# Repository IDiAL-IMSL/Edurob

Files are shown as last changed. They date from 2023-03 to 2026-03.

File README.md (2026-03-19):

# EduRobV2
[Homepage](https://www.imsl.fh-dortmund.de/mobile-roboter/edurob/)
## Educational robot with support for various drive kinematics

EduRob is a handy mobile robot specially designed for education. Through clever design, it is possible to cover different types of drives such as Mecanum, Omniwheel, and differential drive.



## Detailed information:

[Getting Started](Doc/README.md)

[Partslist](Doc/Partslist/README.md)

[PCB](https://github.com/IDiAL-IMSL/Edurob-PCB)

[CAD](https://github.com/IDiAL-IMSL/Edurob-CAD/README.md)

## Example projects:

[SLAM](Projects/SLAM/README.md)

[Line Follower](https://github.com/blssed/EduRob-LineFollower)

---

## Background

In the robotics lab, there is a wide range of different robots available for use in teaching and for the completion of thesis projects. However, they all share one major disadvantage: they prefer to drive themselves rather than being carried. As a result, their application is limited to the lab itself and adjacent rooms.

Especially for basic training in mobile robotics such as controlling different types of drives (Mecanum, Omniwheel, or differential drive), implementing control tasks, and connecting sensors, the experimental area of the robotics lab is not necessarily required. This led to the requirement of developing a flexible platform that can cover all types of drives, and small enough to be taken in a backpack to the home office.

# Possible configurations

EduRob can be equipped with three or four motors and different types of wheels. The motors can be flexibly reconnected by loosening two screws, and other wheels can be attached to the motor shaft.

## Mecanum 

With four motors at the four outer corners, EduRob can be turned into a robot with a classic Mecanum drive. The driving behavior is thus similar to that of OmniMan and the other Mecanum robots of the IMSL.



## Omniwheel with three wheels (120°)

With three motors, EduRob can simulate the classic omniwheel configuration. Three wheels rotated by 120° each allow for omnidirectional driving behavior.



## Omniwheel with four wheels (90°)

In addition to the classic arrangement with three omniwheels, EduRob can also simulate the special form with four omniwheels. Here, four omniwheels are arranged with a rotation of 90° to each other. In comparison to the Mecanum arrangement, the wheels are rotated by about 45°. In this configuration, EduRob can also be driven omnidirectionally.



## Differential drive or Skid-Steer drive

The driving behavior of the Pioneer robots in the IMSL inventory is made possible by the use of four wheels. Even though the arrangement of the wheels is similar to the Mecanum arrangement, sideways movement is not possible due to the use of classic wheels without freewheeling rollers. In addition to forward and backward movement and rotation around the center of the platform, driving in circular arcs is possible. This type of drive is also called Skid-Steer drive. Due to the 4x4 drive, this configuration is particularly suitable for rough terrain. The absence of freewheeling rollers on the wheels also means they are less likely to become contaminated or blocked.



By using two classic wheels and one or two non-driven Omniwheels, a proper differential drive is also possible. In this case, the rotation point moves to the midpoint between the two driven wheels. While this affects the robot's turning behavior (the front part swings out), it still maintains its limited range of movement (forward, backward, turning, and driving in circles). However, the "off-road" capability is reduced by the reduction to two driven wheels, and the use of Omniwheels increases the risk of contamination of free-rolling rollers.



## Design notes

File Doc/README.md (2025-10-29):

## QUICKSTART TO EDUROB V2

### Installation 

Software required:
- Arduino IDE (https://www.arduino.cc/en/software/) - tested with Arduino IDE 2.3.6
- optional: ROS2 Jazzy (https://docs.ros.org/en/jazzy/) - tested with Ubuntu 24.04 

Integration in Arduino IDE:
1. Clone the Repository and move the included library folders in `Edurob/libraries` to the local library folder of Arduino IDE, for instance `~/Arduino/libraries`
4. Insert "Addition boards manager URL": File → Preferences: `https://espressif.github.io/arduino-esp32/package_esp32_index.json`
5. Select board: Tools → Board →esp32 →`ESP32S3 Dev Module`
6. Select port: Tools → Port → for instance `/dev/ttyACM0`
7. Open the folder `Edurob` and open the Arduino sketch `Edurob.ino` in Arduino IDE
8. Modify the Arduino sketch according to your own preferences (see Usage below)
9. Verify and upload the Arduino sketch via USB-C port on Edurob V2 and hit the reset button on the robot to start the uploaded code

### Usage

Set configuration of the Edurob V2 in lines 6 to 10 of `parameter.h` to to define the kinematics of the robot and only comment out the one selected configuration (ideally matching the wheel configuration of the robot hardware):
```
// Set EduRob Configuration
#define MECANUM
// #define DIFF
// #define OMNI4
// #define OMNI3
```

Set line 4 of  `parameter.h` to disable or enable a wireless connection to ROS2 device (via micro_ros)

- disable: `//#define ROS_EN` 
	
	Add user code in the corresponding segment inside the loop function (lines 665 to 669) of `Edurob.ino`:
	```
	//#############-USER-CODE-START-#####################
  	// double tx = 0.0, ty = 0.0, theta = 0.0;
  	// robotSpeedSetpoint << tx, ty, theta;
	// #############-USER-CODE-END-#####################
	```

- enable: `#define ROS_EN`
	
	Set ROS2 enabled parameters in lines 14 to 19 of `parameter.h`:

	```
	#ifdef ROS_EN
	#define ROS_DOMAIN_ID 1
	#define WIFISSID "ESPNET"
	#define WIFIPASS "espnetwifikey"
	#define AGENT_IP "10.0.101.253"
	#define AGENT_PORT 8888
	```

	- set ROS_DOMAIN_ID (refers to https://docs.ros.org/en/jazzy/Concepts/Intermediate/About-Domain-ID.html)
	- set name and password of wifi
	- set ip address and port of micro_ros_agent on ROS2 Jazzy device in same network

	Installation of micro_ros_agent (refers to https://github.com/micro-ROS/micro_ros_setup) on ROS2 Jazzy device in same network in a ROS2 workspace folder (for instance ~/ros2_ws) in a terminal:

	```
	cd ~/ros2_ws
	sudo apt update
	sudo apt install python3-rosdep
	git clone -b jazzy https://github.com/micro-ROS/micro_ros_setup.git src/micro_ros_setup
	rosdep update && rosdep install --from-paths src --ignore-src -y
	sudo rosdep init
	rosdep update
	colcon build --symlink-install
	source install/local_setup.bash
	ros2 run micro_ros_setup create_agent_ws.sh
	ros2 run micro_ros_setup build_agent.sh
	source install/local_setup.bash
	```

	Start of micro_ros_agent on ROS2 Jazzy device with udp4 and defined AGENT_PORT parameters in a terminal:

	```
	ros2 run micro_ros_agent micro_ros_agent udp4 --port 8888
	```

	The terminal should output:

	```
	[1761729504.052943] info     | UDPv4AgentLinux.cpp | init                     | running...             | port: 8888
	[1761729504.055070] info     | Root.cpp           | set_verbose_level        | logger setup           | verbose_level: 4
	```

	Press the reset button on the robot. The terminal output will change if successful:

	```
	[1761729504.052943] info     | UDPv4AgentLinux.cpp | init                     | running...             | port: 8888
	[1761729504.055070] info     | Root.cpp           | set_verbose_level        | logger setup           | verbose_level: 4
	[1761729843.354045] info     | Root.cpp           | create_client            | create                 | client_key: 0x7A4912AF, session_id: 0x81
	[1761729843.355923] info     | SessionManager.hpp | establish_session        | session established    | client_key: 0x7A4912AF, address: 10.0.109.1:47138
	[1761729843.510983] info     | ProxyClient.cpp    | create_participant       | participant created    | client_key: 0x7A4912AF, participant_id: 0x000(1)
	[1761729843.574304] info     | ProxyClient.cpp    | create_topic             | topic created          | client_key: 0x7A4912AF, topic_id: 0x000(2), participant_id: 0x000(1)
	[1761729843.586440] info     | ProxyClient.cpp    | create_subscriber        | subscriber created     | client_key: 0x7A4912AF, subscriber_id: 0x000(4), participant_id: 0x000(1)
	[1761729843.594849] info     | ProxyClient.cpp    | create_datareader        | datareader created     | client_key: 0x7A4912AF, datareader_id: 0x000(6), subscriber_id: 0x000(4)
	[1761729843.601925] info     | ProxyClient.cpp    | create_topic             | topic created          | client_key: 0x7A4912AF, topic_id: 0x001(2), participant_id: 0x000(1)
	[1761729843.607856] info     | ProxyClient.cpp    | create_publisher         | publisher created      | client_key: 0x7A4912AF, publisher_id: 0x000(3), participant_id: 0x000(1)
	[1761729843.614818] info     | ProxyClient.cpp    | create_datawriter        | datawriter created     | client_key: 0x7A4912AF, datawriter_id: 0x000(5), publisher_id: 0x000(3)
	```

	The ROS2 terminal command `ros2 topic list` will show:

	```
	/cmd_vel
	/parameter_events
	/rosout
	/tf
	```

	The ROS2 terminal command `ros2 node list` will output `/EduRob_Node`. A following command `ros2 node info /EduRob_Node` will show that the node `/EduRob_Node` subscribed to the topic `/cmd_vel` and publishes the topic `/tf` as seen in the topic list before:

	```
	/EduRob_Node
	  Subscribers:
		/cmd_vel: geometry_msgs/msg/Twist
	  Publishers:
		/tf: tf2_msgs/msg/TFMessage
	```

	Since transformations are published via `/tf` and driving commands are sent in ROS2 via `/cmd_vel`, the robot is ready to be controlled, among other things, via a teleoperation node such as teleop_twist_keyboard.

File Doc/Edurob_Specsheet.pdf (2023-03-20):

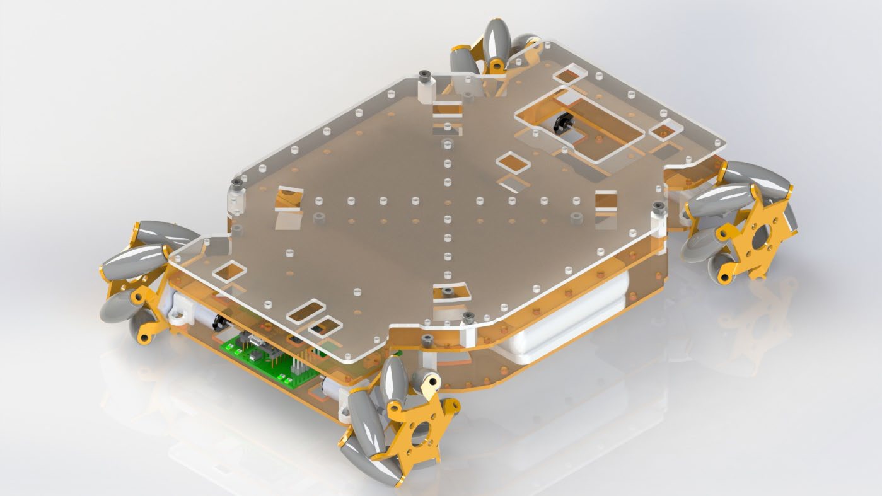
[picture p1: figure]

[1/4] | Edurob Datasheet | REV.: 1.1.0

# Edurob

Educational robot with support for various drive kinematics

## Features

- Espressif ESP32 Microcontroller
- Dual core, 240Mhz, 32bit
- Connectivity
- Wifi (2.4Ghz, 802.11b/g/n)
- Bluetooth 4.2
- USB UART (3Mbaud)
- I²C Fast mode (400 Kbit/s, 3.3V)
- Input/Output
- 4 Motor PWM Outputs
- 4 Encoder Inputs (3.3V)
- 8 GPIOs (3.3V)
- Stackable Design
- Dimensions without wheels
- 160mm x 240mm x 30mm
- Input Voltage Range
- 5VDC Power Supply (USB
Powerbank)
- 3.3V Logic voltage level
- Software capabilities
- ROS2 Interface (MicroROS)
- Motor control
- Velocity
- Position
- Supported Robot kinematics
- Omnidirectional
Mecanum
- Omnidirectional
Omniwheel
- Differential

Educational robot with support for various drive kinematics

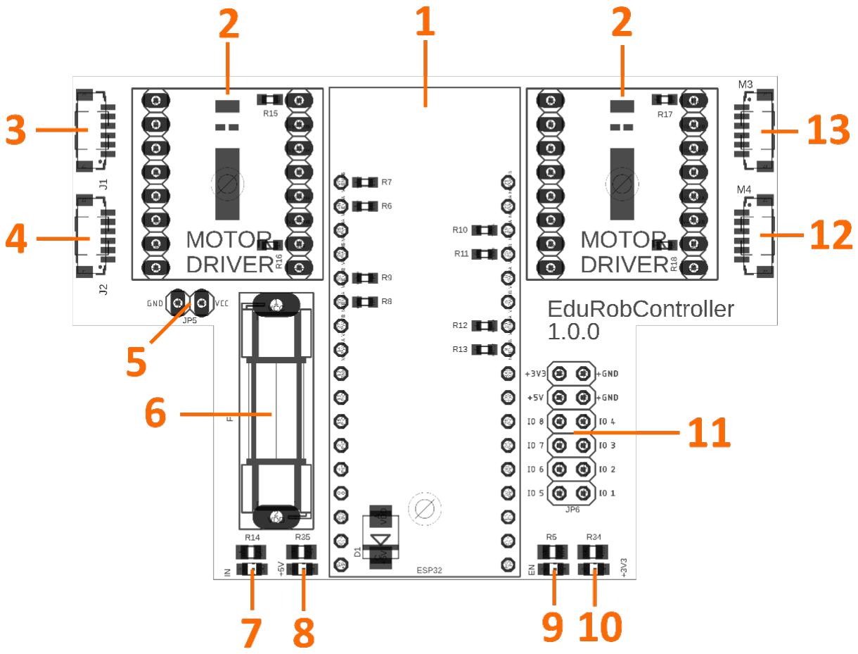
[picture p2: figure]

1 | ESP32-PICO-KIT | 8 | USB Voltage Indicator
2 | Dual DC Motordriver TB6612FNG (1A) | 9 | Motor Enable Indicator
3 | Motor 3 connector | 10 | Logic Voltage Indicator
4 | Motor 1 connector | 11 | GPIO Header
5 | Supply Voltage Connector (max. 5VDC) | 12 | Motor 0 connector
6 | 5x20 Fuse (4A) | 13 | Motor 2 connector
7 | Supply Voltage Indicator

Educational robot with support for various drive kinematics

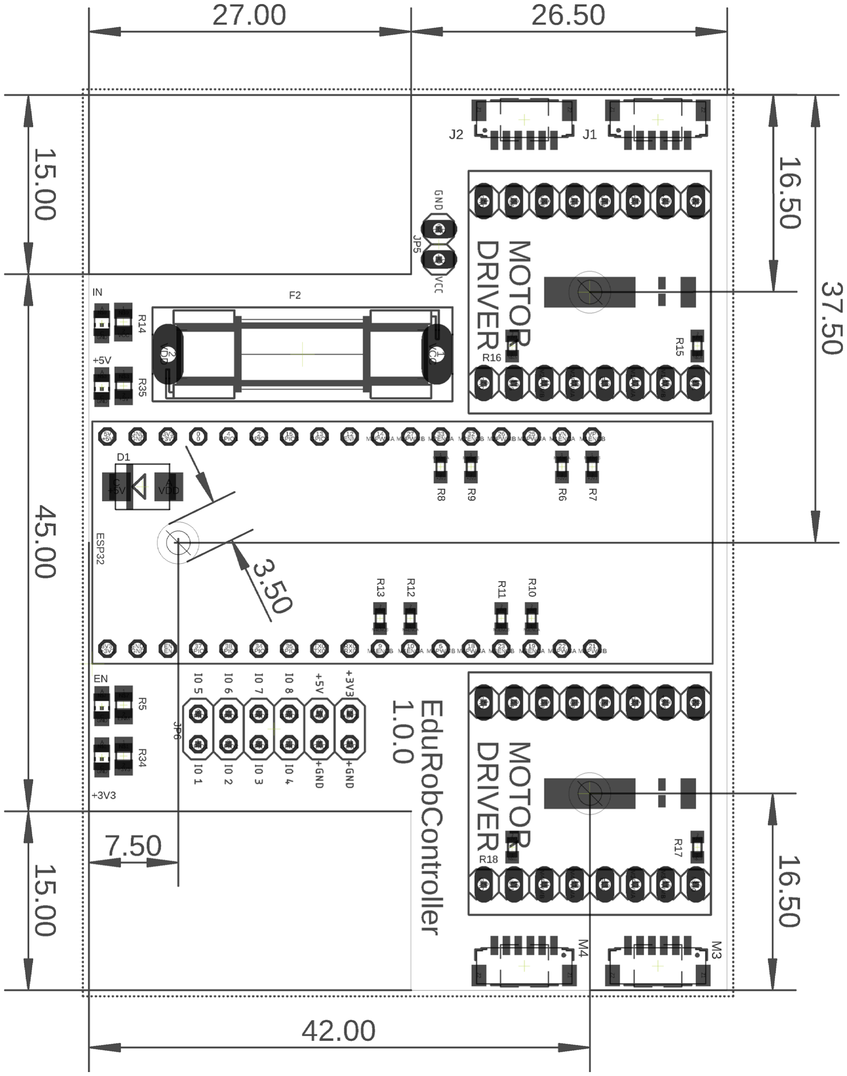
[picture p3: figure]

Educational robot with support for various drive kinematics

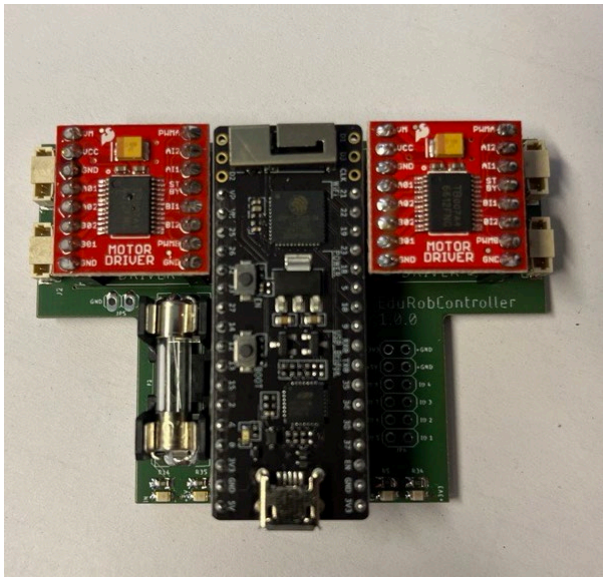
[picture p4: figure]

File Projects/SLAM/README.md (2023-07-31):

# EduRob SLAM
[Homepage](https://www.imsl.fh-dortmund.de/mobile-roboter/edurob/)
## Project files for SLAM with EduRob

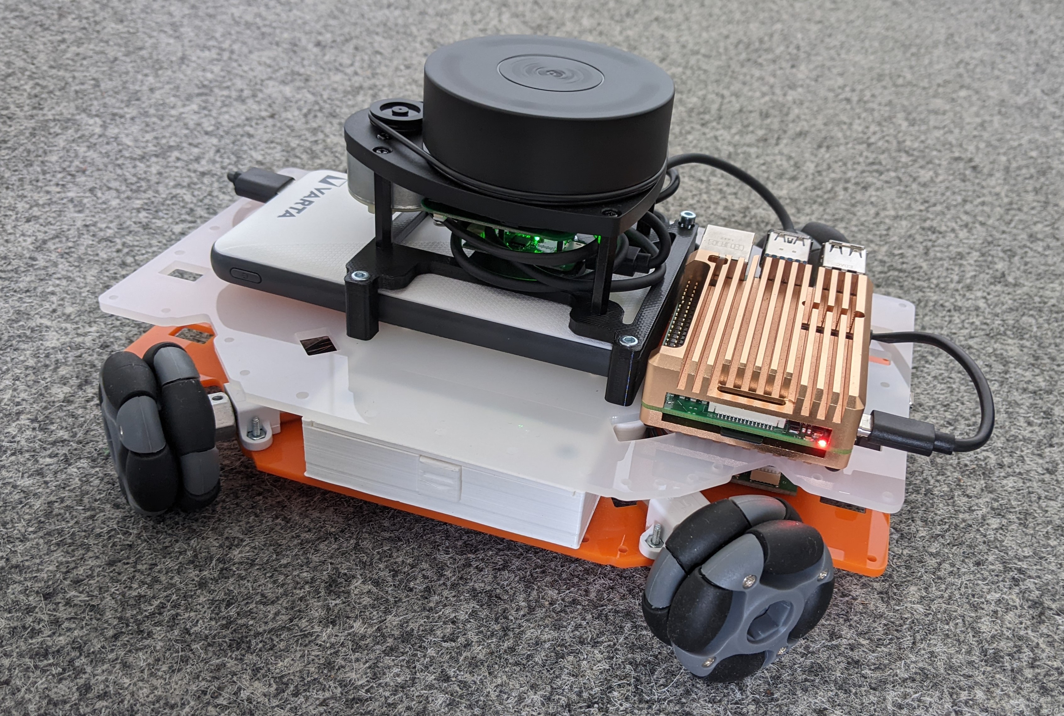
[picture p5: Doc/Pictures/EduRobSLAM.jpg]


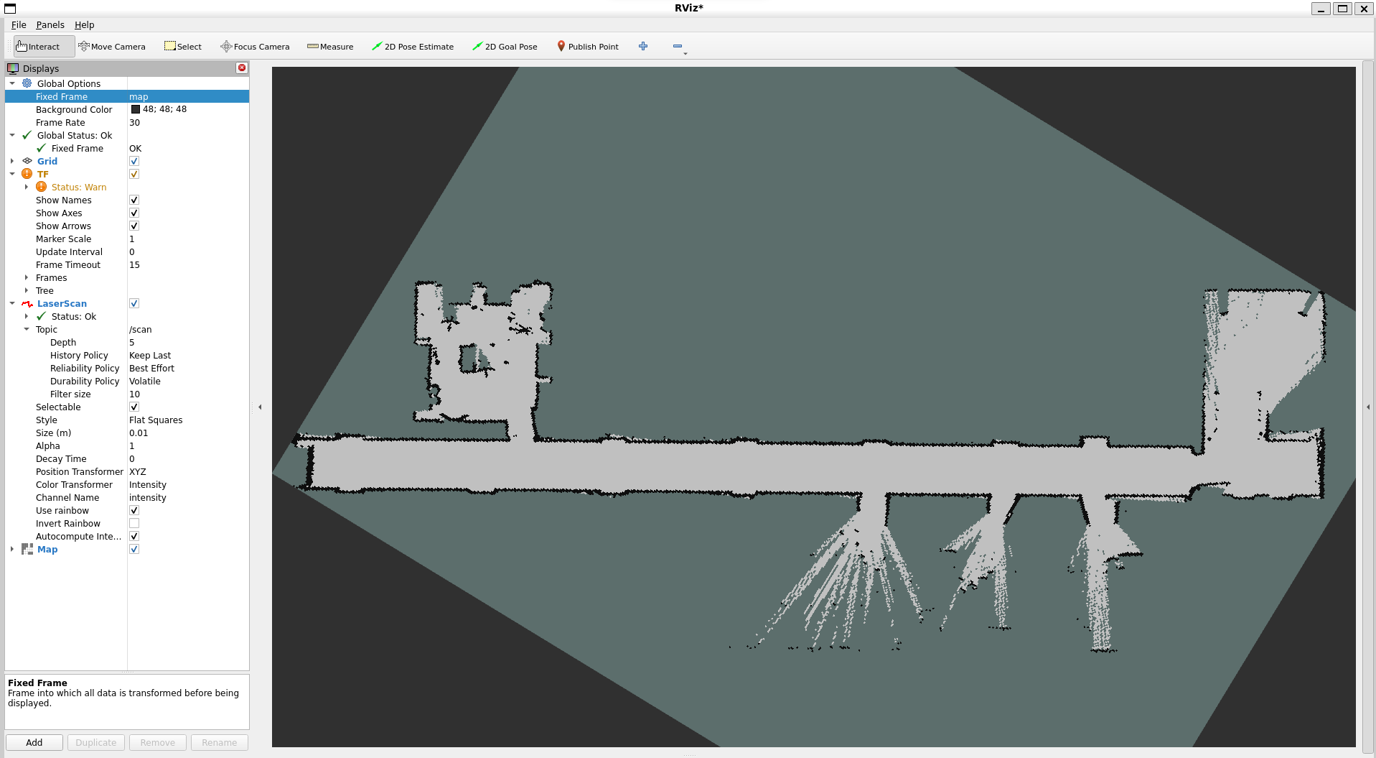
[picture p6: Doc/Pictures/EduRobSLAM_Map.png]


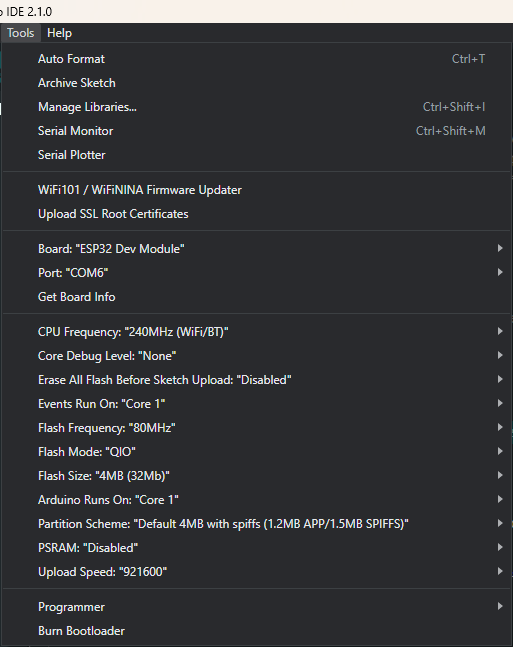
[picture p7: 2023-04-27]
Doc/Pictures/ArduinoConfig.png

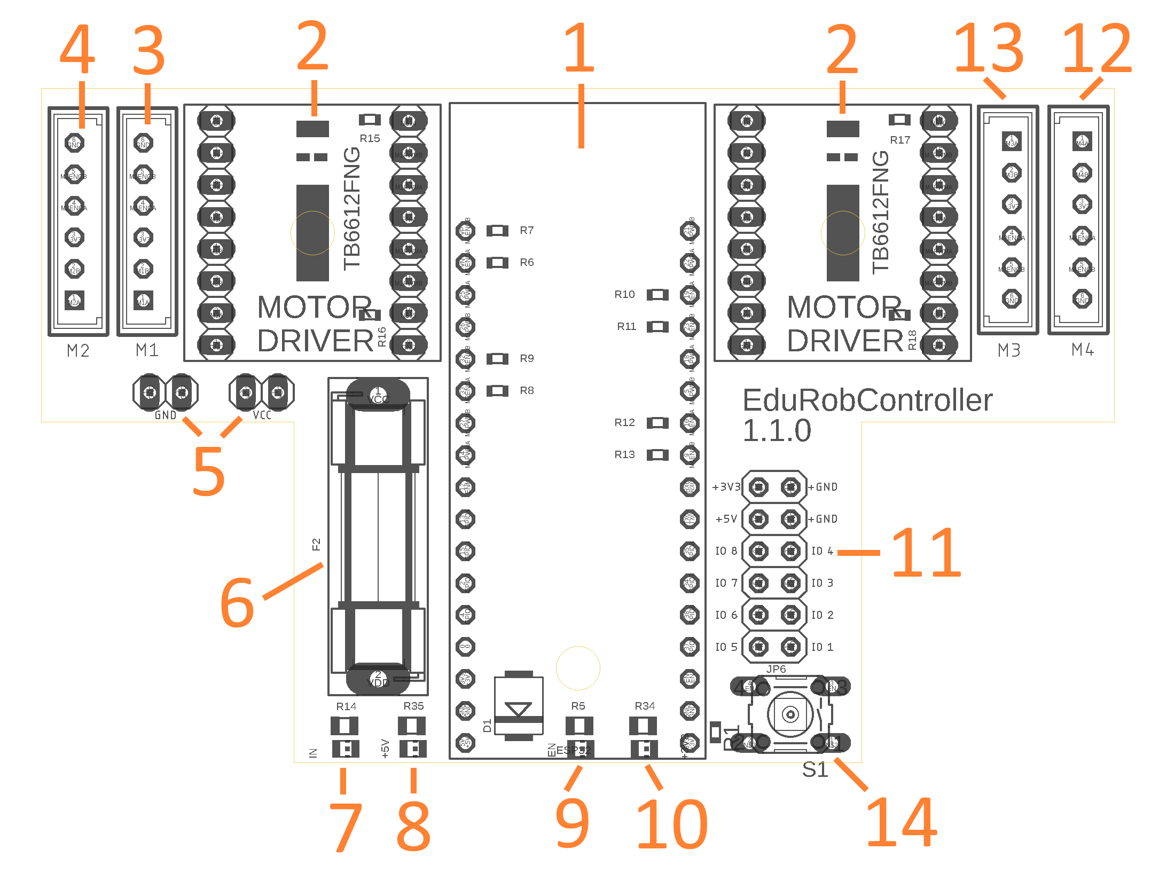
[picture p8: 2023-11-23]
Doc/Pictures/pcb_img_num.png

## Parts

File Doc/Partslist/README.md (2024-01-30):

# EduRob Partslist
[Homepage](https://www.imsl.fh-dortmund.de/mobile-roboter/edurob/)
## List of necessary items to build your own EduRob

---
|No.| Device | Number | URL |
|:---:|:---:|:---:|:---:|
| 1 |Adafruit N20 DC Motor with Magnetic Encoder - 6V with 1:100 Gear Ratio| 4 | [Link](https://www.mouser.de/ProductDetail/Adafruit/4639?qs=DPoM0jnrROWCfj%252BnzBxvKw%3D%3D)  |
| 2 | 48mm Steel Mecanum Wheel Set (2x Left, 2x Right)  | 1 | [Link](https://eu.robotshop.com/products/48mm-steel-mecanum-wheel-set-2x-left-2x-right)  |
| 3 | 48mm Omni Wheel for Hex Hub  |4| [Link](https://eu.robotshop.com/products/48mm-omni-wheel-hex-hub)  |
| 4 | Varta Power Bank Energy 10000 Powerbank  |1| [Link](https://www.conrad.de/de/p/varta-power-bank-energy-10000-powerbank-10000-mah-lipo-usb-c-weiss-schwarz-2338727.html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)  |
| 5 | Motor Driver - Dual TB6612FNG v2 (w/ Headers)  |2| [Link](https://eu.robotshop.com/products/motor-driver-dual-tb6612fng-v2-headers)|
| 6 | Plug, right angle Plug, right angle Typ A 90° USB type A plug, 90° 774866 TRU COMPONENTS  |2| [Link](https://www.conrad.com/p/plug-right-angle-plug-right-angle-typ-a-90-usb-type-a-plug-90-774866-tru-components-content-1-pcs-1567163)|
| 7 | EduRob_Baseplate  |1 or more| [Link](/CAD/EduRob_Baseplate.STEP)|
| 8 | EduRobController  |1| [Link](/Doc/Partslist/README.md)|
| 9 | M4 10mm DIN912 screw  | 4 | |
| 10 | M2 10mm DIN912 screw  | 16 | |
| 11 | M3 10mm DIN912 screw  | 8 | |
| 12 | M3 6mm DIN912 screw  | 3 | |
| 13 | M3 6mm Grub screw  | 4-12 | |

---
## List of necessary 3D-printed files

|No.| Device | Number | URL |
|:---:|:---:|:---:|:---:|
| 1 | EduRob_Baseplate |1 or more| [Link](/CAD/EduRob_Baseplate.STEP)|
| 2 | EduRob_Battery_Compartment_Main |1 | [Link](/CAD/EduRob_Battery_Compartment_Main.STEP)|
| 3 | EduRob_Battery_Compartment_Lid |1 | [Link](/CAD/EduRob_Battery_Compartment_Lid.STEP)|
| 4 | EduRob_Battery_Compartment_EjectB |1 | [Link](/CAD/EduRob_Battery_Compartment_EjectB.STEP)|
| 5 | Edurob_Mecanum_Adapter |4 | [Link](/CAD/Edurob_Mecanum_Adapter.step)|
| 6 | Edurob_Motor_Mount |4 | [Link](/CAD/Edurob_Motor_Mount.step)|

---
## List of necessary items to build one EduRobController

|No.| Device | Number | URL |
|:---:|:---:|:---:|:---:|
| 1 | SMD 10k resistor 0603 | 13 | |
| 2 | SMD 300R resistor 0805 | 4 | |
| 3 | SMD LED orange 0805 (Vf = 2V) | 4 | |
| 4 | Schottky-Diode SMB|1| |
| 5 | Fuse-Holder 5mmx20mm (e.g. Keystone Electronics 4628) | 1 | [Link](https://eu.mouser.com/ProductDetail/Keystone-Electronics/4628?qs=zfzUrXoPZmjT%252BZ7zWJhosA%3D%3D) |
| 6 | Tactile switch (B3F-10XX) | 1 | |
| 7 | ESP32-PICO-KIT | 1 | [Link](https://www.mouser.de/ProductDetail/Espressif-Systems/ESP32-PICO-KIT-1?qs=HoCaDK9Nz5ccXDqscvfzVw%3D%3D) |
| 8 | Board-Connector B6B-EH-A (optional) | 4 | [Link](https://www.reichelt.de/jst-stiftleiste-rm-2-5-mm-1x6-polig-gerade-eh-jst-eh6p-st-p190551.html) |
| 9 | Wire-Connector B6B-EH-A (optional) | 4 | [Link](https://www.conrad.at/de/p/jst-buchsengehaeuse-kabel-eh-polzahl-gesamt-6-ehr-6-1-st-1217311.html) |
| 10 | Connector contacts B6B-EH-A (optional) | 24 | [Link](https://www.conrad.at/de/p/jst-crimpkontakt-eh-beh-001t-p0-6-1-st-1217316.html) |
| 11 | PCB |1 | [Link](/PCB/README.md)

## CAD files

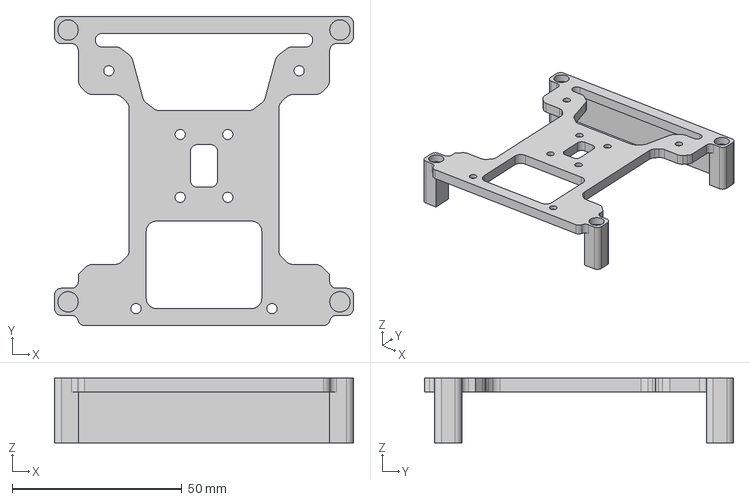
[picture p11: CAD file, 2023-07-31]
Projects/SLAM/LIDAR_Adapter v5.step
88.0 x 91.0 x 19.0 mm

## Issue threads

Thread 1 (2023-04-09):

Smartcar shield/ software collaboration

samuk, 2023-04-09:
Hi I was wondering if you had seen https://github.com/platisd/smartcar_shield#software

Dual driver support was recently added to support this project I'm working on: https://rosmo-robot.github.io/

Collaboration on the software side would be welcome.

samuk, 2023-05-27:
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

Did a little playing around with your PCB so it could optionally be used as a 2WD bot without the housing.

I think it would still fit in your robot for the 4x4 configurations.

Some ideas I've been playing with
- Change to the 40pinRPI Pico footprint for more MCU flexibility.
- Add a [Mikro footprint ](https://www.mikroe.com/click) for additional sensors

samuk, 2023-08-14:
I spotted you'd started some ROS stuff. Do you know this project that provides ESP32 > ROS2 compatibility with Wifi transport https://github.com/hippo5329/linorobot2_hardware

xXAM22Xx, 2023-08-15:
Hi, the projects you mentioned are really interesting. We'll definitely keep an eye on them. Our robot is completely compatible with ROS2 via Microros. You can either use a Wifi connection to a computer on the same network or a Serial connection via USB to a Raspberry Pi. As you may have seen we are currently working on different sensor addons and use cases so we can improve the current design of the robot in a future revision. The PCB you have designed looks great. I like the idea of a PCB as a chassis. I've added a PCB-only design of the Edurob to my ToDo list and would keep you updated when I start working on it.

samuk, 2023-08-15:
Do have a look at the ESP32 Linorobot fork above. I think it may be useful to you. It would be great to see your development efforts supporting and enhancing the existing community around that codebase.

I'm quite into this new project/ hardware https://experientialrobotics.org/

I'm hoping I can get wifi transport working on the RP2040. If I can I'll add some linorobot2/ ros2 stuff to their docs: https://introtoroboticsv2.readthedocs.io/en/latest/

You might also be interested in this meeting tomorrow? https://discourse.ros.org/t/first-education-working-group-meeting/32819/1

samuk, 2023-09-30:
I've been following this thread a bit and got to here: https://rosmo-robot.github.io/zio/

I've decided to work with this open hardware driver for a while https://www.smart-prototyping.com/Zio-4-DC-Motor-Controller.html?search=motor quite similar to your setup

WIP code is here https://github.com/rosmo-robot/linorobot2_hardware_hippo_esp32_fix

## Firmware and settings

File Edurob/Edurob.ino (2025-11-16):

/**************************************************************************
 * Edurob Arduino Project
 *
 * This project controls a robotic platform using ESP32-based hardware.
 * It facilitates motor control, encoder feedback, PID speed regulation,
 * kinematics calculations, and ROS2 communication for velocity commands
 * and transform publishing.
 *
 * Hardware components:
 * - Motors with PWM control
 * - Encoders for wheel speed and direction feedback
 * - ESP32 microcontroller with FreeRTOS
 *
 * Software components:
 * - PID controllers for motor speed regulation
 * - Kinematics matrices to translate robot motions to wheel speeds
 * - ROS2 micro-ROS support for command and sensor messaging
 *
 **************************************************************************/

// Project specific parameters
#include "parameter.h"


#include <WiFi.h>
#include "sdkconfig.h"
#include "esp_system.h"
#include "freertos/FreeRTOS.h"
#include "freertos/task.h"
#include "freertos/timers.h"
#include "freertos/event_groups.h"
#include "math.h"

// Hardware and control libraries for PWM, Encoder, PID control, and matrix math
#include <dcpwm.h>       // PWM
#include <ESP_Counter.h> // Encoder
#include <AutoPID.h>     // PID Library https://github.com/r-downing/AutoPID
#include <Eigen.h>       // Linear math
#include <Eigen/QR>      // Calls inverse, determinant, LU decomp., etc.
using namespace Eigen;   // Simplify matrix/vector declarations

// ROS
#ifdef ROS_EN
// Include micro-ROS headers for communication and message definitions
#include <micro_ros_arduino.h>
#include <stdio.h>
#include <rcl/rcl.h>
#include <rcl/error_handling.h>
#include <rclc/rclc.h>
#include <rclc/executor.h>
#include <rosidl_runtime_c/string_functions.h>

// ROS Messages
#include <geometry_msgs/msg/twist.h>
#include <tf2_msgs/msg/tf_message.h>
#include <nav_msgs/msg/odometry.h>
#include <geometry_msgs/msg/transform_stamped.h>

// Error checking macros for ROS functions
#define RCCHECK(fn)              \
  {                              \
    rcl_ret_t temp_rc = fn;      \
    if ((temp_rc != RCL_RET_OK)) \
    {                            \
      error_loop();              \
    }                            \
  }
#define RCSOFTCHECK(fn)          \
  {                              \
    rcl_ret_t temp_rc = fn;      \
    if ((temp_rc != RCL_RET_OK)) \
    {                            \
      error_loop_soft();         \
    }                            \
  }

// ROS communication variables
rcl_subscription_t subscriber;
rcl_publisher_t tf_pub;
geometry_msgs__msg__Twist msg;
geometry_msgs__msg__TransformStamped tfMessages[2]; // Transform between base_link / odom and base_link / laser
tf2_msgs__msg__TFMessage tf2Message;
rclc_executor_t executor;
rcl_allocator_t allocator;
rcl_init_options_t init_options;
rclc_support_t support;
rcl_node_t node;
rcl_timer_t timer;
unsigned int timer_timeout1;
geometry_msgs__msg__Quaternion q;

#endif // ROS_EN

// kinematik header
#include "kinematik.h"

// Hardware-related global objects
static ESP_Counter WheelEncoder[NumMotors];      // Encoder hardware interfaces
static DCPWM MotorPWM[NumMotors];                // PWM hardware interfaces
static AutoPID *speedController[NumMotors];      // PID controller instances
static pidParam speedControllerParam[NumMotors]; // PID parameters per motor

// Encoder and filtering variables
int64_t encoderOld[NumMotors];       // Previous encoder counts for velocity calculation
int64_t encoderNew[NumMotors];       // Current encoder counts
const int windowSize = 5;            // Size for moving average filter
float inputs[NumMotors][windowSize]; // Recent velocity samples per motor
float inputsum[NumMotors];           // Summed filter inputs for average calculation
int windowIndex = 0;                 // Circular index for moving average buffer

// Setpoint and kinematics variables
static double setpointSpeed[NumMotors]; // Speed setpoints per motor
MatrixXd kinematik(4, 3);    // Forward kinematics matrix
MatrixXd kinematikInv(3, 4); // Inverse kinematics matrix
Vector3d robotSpeedSetpoint; // Desired robot speed [m/s rad/s]
Vector3d robotSpeed;         // Current robot speed
Vector3d robotSpeedMax;      // Max allowed robot speed
Vector3d robotSpeedAcc;      // Robot speed acceleration limits
Vector4d wheelSpeedSetpoint; // Desired wheel speeds [rad/s]
Vector3d robotOdom;          // Odometry position (x, y, theta)
Vector4d robotWheelSpeed;    // Current wheel velocities
double rosQuaternion[4];     // Quaternion for ROS transform messages



/**************************** Function Definitions ****************************/

// ROS
#ifdef ROS_EN

/**
 * @brief ROS subscriber callback to update velocity setpoints from command messages.
 * 
 * @param msgin Pointer to the incoming Twist message.
 */
void subscription_callback(const void *msgin)
{
  const geometry_msgs__msg__Twist *msg = (const geometry_msgs__msg__Twist *)msgin;

  // Update robot speed setpoints for linear and angular velocities
  robotSpeedSetpoint << msg->linear.x, msg->linear.y, msg->angular.z;
}

/**
 * @brief ROS task that publishes TF transforms to ROS in a loop.
 * 
 * This task publishes odometry and laser transforms periodically.
 * 
 * @param pvParameters FreeRTOS task parameters (unused)
 */
void ros_task(void *pvParameters)
{

  while (1)
  {
    vTaskDelay(pdMS_TO_TICKS(10));
    
    // Convert yaw (theta) from robot odometry into a quaternion
    double quat[4];
    euler_to_quat(0, 0, robotOdom[2], quat);

    // Setup odom->base_link transform
    tfMessages[0].child_frame_id.data = "base_link";
    tfMessages[0].transform.translation.x = robotOdom[0];
    tfMessages[0].transform.translation.y = robotOdom[1];
    tfMessages[0].transform.translation.z = 0;
    tfMessages[0].transform.rotation.x = quat[1];
    tfMessages[0].transform.rotation.y = quat[2];
    tfMessages[0].transform.rotation.z = quat[3];
    tfMessages[0].transform.rotation.w = quat[0];
    tfMessages[0].header.frame_id.data = "odom";
    tfMessages[0].header.stamp.sec = rmw_uros_epoch_millis() / 1000;
    tfMessages[0].header.stamp.nanosec = rmw_uros_epoch_nanos();

    // Setup base_link->laser transform
    tfMessages[1].child_frame_id.data = "laser";
    tfMessages[1].transform.translation.x = 0;
    tfMessages[1].transform.translation.y = 0;
    tfMessages[1].transform.translation.z = 0.08;
    tfMessages[1].transform.rotation.x = 0;
    tfMessages[1].transform.rotation.y = 0;
    tfMessages[1].transform.rotation.z = 0;
    tfMessages[1].transform.rotation.w = 1;
    tfMessages[1].header.frame_id.data = "base_link";
    tfMessages[1].header.stamp.sec = rmw_uros_epoch_millis() / 1000;
    tfMessages[1].header.stamp.nanosec = rmw_uros_epoch_nanos();

    // Configure TF message container
    tf2Message.transforms.capacity = 2;
    tf2Message.transforms.data = tfMessages;
    tf2Message.transforms.size = 2;

    // Publish TF message to ROS, handle errors softly
    RCSOFTCHECK(rcl_publish(&tf_pub, &tf2Message, NULL));
  }
}

#endif // ROS_EN

/**
 * @brief Infinite error loop triggered on fatal ROS errors.
 * 
 * Prints "FATAL ROS ERROR ABORTING" to serial console continuously.
 */
void error_loop()
{
  while (1)
  {
    Serial.println("FATAL ROS ERROR ABORTING");
    delay(1000);
  }
}

/**
 * @brief Soft error handler prints "SOFT ROS ERR" once.
 */
void error_loop_soft()
{
  Serial.println("SOFT ROS ERR");
}

#ifdef ROS_EN
/**
 * @brief Converts Roll-Pitch-Yaw Euler angles to a ROS quaternion message.
 * 
 * @param roll Roll angle in radians.
 * @param pitch Pitch angle in radians.
 * @param yaw Yaw angle in radians.
 * @return geometry_msgs__msg__Quaternion Constructed quaternion message.
 */
static geometry_msgs__msg__Quaternion createQauternionFromRPY(double roll, double pitch, double yaw)
{
  geometry_msgs__msg__Quaternion q;
  double halfYaw = yaw * 0.5;
  double halfPitch = pitch * 0.5;
  double halfRoll = roll * 0.5;
  double cosYaw = cos(halfYaw);
  double sinYaw = sin(halfYaw);
  double cosPitch = cos(halfPitch);
  double sinPitch = sin(halfPitch);
  double cosRoll = cos(halfRoll);
  double sinRoll = sin(halfRoll);
  q.x = sinRoll * cosPitch * cosYaw - cosRoll * sinPitch * sinYaw; // x
  q.y = cosRoll * sinPitch * cosYaw + sinRoll * cosPitch * sinYaw; // y
  q.z = cosRoll * cosPitch * sinYaw - sinRoll * sinPitch * cosYaw; // z
  q.w = cosRoll * cosPitch * cosYaw + sinRoll * sinPitch * sinYaw; // formerly yzx
  return q;
}
#endif // ROS_EN

/**
 * @brief Converts Euler angles (degrees) to a quaternion array.
 * 
 * @param x Roll angle [degrees]
 * @param y Pitch angle [degrees]
 * @param z Yaw angle [degrees]
 * @param q Output array to store quaternion [w, x, y, z]
 */
const void euler_to_quat(float x, float y, float z, double *q)
{
  float c1 = cos(y / 2.0);
  float c2 = cos(z / 2.0);
  float c3 = cos(x / 2.0);

  float s1 = sin(y / 2.0);
  float s2 = sin(z / 2.0);
  float s3 = sin(x / 2.0);

  q[0] = c1 * c2 * c3 - s1 * s2 * s3; // w
  q[1] = s1 * s2 * c3 + c1 * c2 * s3; // x
  q[2] = s1 * c2 * c3 + c1 * s2 * s3; // y
  q[3] = c1 * s2 * c3 - s1 * c2 * s3; // z
}

/**
 * @brief Checks direction of rotation of encoder.
 * 
 * Samples encoder counts twice with delay and determines if count is increasing
 * or decreasing, indicating direction.
 * 
 * @param encoder Reference to encoder hardware interface (ESP_Counter).
 * @return int 1 = forward (count increased), -1 = reverse (count decreased), 0 = no change.
 */
int checkEncoderDirection(ESP_Counter &encoder)
{
  int count = encoder.getCount();
  delay(50);
  int count2 = encoder.getCount();
  if (count2 > count)
  {
    return 1;
  }
  else if (count2 < count)
  {
    return -1;
  }
  else
  {
    return 0;
  }
}

/**
 * @brief Rotates a 2D vector by angle r (radians).
 * 
 * Applies rotation matrix multiplication to update coordinates in place.
 * 
 * @param r Rotation angle in radians
 * @param x Reference to x component, updated in place
 * @param y Reference to y component, updated in place
 */
const void rotate2D(float r, double &x, double &y)
{
  double temp = x * cos(r) - y * sin(r);
  y = x * sin(r) + y * cos(r);
  x = temp;
}

/**
 * @brief Prints contents of an Eigen matrix to the serial console.
 * 
 * Useful for debug logging matrix values step-by-step.
 * 
 * @param X MatrixXd reference to print.
 */
void print_mtxd(const Eigen::MatrixXd &X)
{
  int i, j, nrow, ncol;

  nrow = X.rows();
  ncol = X.cols();

  Serial.print("nrow: ");
  Serial.println(nrow);
  Serial.print("ncol: ");
  Serial.println(ncol);
  Serial.println();

  for (i = 0; i < nrow; i++)
  {
    for (j = 0; j < ncol; j++)
    {
      Serial.print(X(i, j), 6); // print 6 decimal places
      Serial.print(", ");
    }
    Serial.println();
  }
  Serial.println();
}

/**
 * @brief Initialize hardware PWM and encoder peripherals.
 * 
 * Configures pins, initializes encoders and PWM units for motors,
 * determines encoder direction, enables motors and resets counters.
 * 
 * @return true if successful, false if any initialization fails.
 */
bool initHardware()
{
  pinMode(EnablePIN, OUTPUT);   // Motor enable signal
  digitalWrite(EnablePIN, LOW); // Disable motors while initializing
  for (int i = 0; i < NumMotors; i++)
  {
    if (!WheelEncoder[i].init(i, Enc_A[i], Enc_B[i]))
    {
      return false;
    }
  }

  int currentChannel = 0;
  for (int i = 0; i < NumMotors; i++)
  {
    if (!MotorPWM[i].init(30000, 10, currentChannel, currentChannel + 1, PWM_A[i], PWM_B[i]))
    {
      return false;
    }
    MotorPWM[i].setPWM(0); // Set initial speed to 0
    currentChannel += 2;
  }
  digitalWrite(EnablePIN, HIGH); // Enable motors
  for (int i = 0; i < NumMotors; i++)
  {
    MotorPWM[i].setPWM(100 * MotorDir[i]); // Briefly run to confirm encoder direction
    EncoderDir[i] = checkEncoderDirection(WheelEncoder[i]);
    MotorPWM[i].setPWM(0);
  }
  delay(1000); // Allow counts to stabilize
  for (int i = 0; i < NumMotors; i++)
  {
    WheelEncoder[i].resetCounter();
  }

  return true;
}

/**
 * @brief Initialize PID speed controllers with default parameters.
 * 
 * Sets PID gains, sampling time, output limits for each motor's speed control.
 */
void initPID()
{
  for (int i = 0; i < NumMotors; i++)
  {
    speedControllerParam[i].input = 0;
    speedControllerParam[i].output = 0;
    speedControllerParam[i].setpoint = 0;
    speedControllerParam[i].p = 0.04;
    speedControllerParam[i].i = 0.08;
    speedControllerParam[i].d = 0.0;
    speedControllerParam[i].sampleTimeMs = sampleTime;
    speedControllerParam[i].outMin = -100;
    speedControllerParam[i].outMax = 100;

    speedController[i] = new AutoPID(&speedControllerParam[i].input, &speedControllerParam[i].setpoint, &speedControllerParam[i].output, speedControllerParam[i].outMin, speedControllerParam[i].outMax, speedControllerParam[i].p, speedControllerParam[i].i, speedControllerParam[i].d);
    speedController[i]->setTimeStep(speedControllerParam[i].sampleTimeMs);
    speedController[i]->setBangBang(0, 0); // Disable BangBang-Controll
  }
}

/**
 * @brief Initialize kinematic matrices depending on robot type.
 * 
 * Sets forward and inverse kinematics matrices for robot motion translation.
 * Sets initial speed vectors and acceleration/speed limits.
 */
void initMatrix()
{

#ifdef MECANUM
  // Mecanum
  mecanum_matrix(kinematik, kinematikInv, l1, l2); // sets the kinematik and kinematikInv to the desired values
#endif

#ifdef DIFF
  // Diff
  differential_matrix(kinematik, kinematikInv, l1, l2); // sets the kinematik and kinematikInv to the desired values

#endif

#ifdef OMNI4
  // Omni 4 Wheels
  omni_4_matrix(kinematik, kinematikInv, l1, l2); // sets the kinematik and kinematikInv to the desired values
#endif

#ifdef OMNI3
  // Omni 3 Wheels
  omni_3_matrix(kinematik, kinematikInv, l1, l2); // sets the kinematik and kinematikInv to the desired values
#endif

  robotSpeedSetpoint << 0.0,
      0.0,
      0.0;

  robotSpeedAcc << maxTAccel, maxTAccel, maxRAccel;
  robotSpeedMax << maxTSpeed, maxTSpeed, maxRSpeed;
  wheelSpeedSetpoint = (1 / wheelRadius) * kinematik * robotSpeedSetpoint;
}

/**
 * @brief FreeRTOS task that runs the speed controller loop.
 * 
 * Applies PID control for motor speeds using encoder feedback and setpoints.
 * Updates robot odometry estimates.
 * 
 * @param pvParameters Task parameters (unused)
 */
void speedControllerTask(void *pvParameters)
{
  TickType_t xLastWakeTime = xTaskGetTickCount();
  const TickType_t xFrequency = pdMS_TO_TICKS(sampleTime);
  Vector4d EncoderRadDiff;
  Vector3d robotOdomChange;
  Vector3d worldOdomChange;

  for (int i = 0; i < NumMotors; i++)
  {
    inputsum[i] = 0;
  }

  for (int i = 0; i < NumMotors; i++)
  {
    for (int k = 0; k < windowSize; k++)
    {
      inputs[i][k] = 0;
    }
  }

  while (true)
  {
    vTaskDelayUntil(&xLastWakeTime, xFrequency);

    // Adjust current robot speeds to setpoints respecting velocity limits
    for (int i = 0; i < 3; i++)
    {
      robotSpeed[i] = robotSpeedSetpoint[i];

      // Clamp to max speeds
      if (robotSpeed[i] > robotSpeedMax[i])
      {
        robotSpeed[i] = robotSpeedMax[i];
      }
      else if (robotSpeed[i] < -robotSpeedMax[i])
      {
        robotSpeed[i] = -robotSpeedMax[i];
      }

      // Zero small speeds for stability
      if (robotSpeed[i] < 0.000001 && robotSpeed[i] > -0.000001)
      {
        robotSpeed[i] = 0;
      }
    }

    // Calculate wheel speed setpoints with kinematics matrix
    wheelSpeedSetpoint = (1 / wheelRadius) * kinematik * robotSpeed;

    // Deadzone elimination for minimal wheel speeds
    for (int i = 0; i < NumMotors; i++)
    {
      if (abs(wheelSpeedSetpoint[i]) < 0.15)
      {
        wheelSpeedSetpoint[i] = 0;
      }
    }

    // Set PID controller setpoints for each motor
    for (int i = 0; i < NumMotors; i++)
    {
      speedControllerParam[i].setpoint = wheelSpeedSetpoint(i, 0);
    }

    // Update encoder readings and filtered speed inputs
    for (int i = 0; i < NumMotors; i++)
    {
      encoderNew[i] = EncoderDir[i] * WheelEncoder[i].getCount();

      // Get the increments since last run
      EncoderRadDiff[i] = (encoderNew[i] - encoderOld[i]) * incrementsToRad;

      inputsum[i] -= inputs[i][windowIndex];
      inputs[i][windowIndex] = ((((encoderNew[i] - encoderOld[i]) * incrementsToRad) / sampleTime) * 1000);
      inputsum[i] += inputs[i][windowIndex];

      speedControllerParam[i].input = inputsum[i] / windowSize; // Moving average filter

      speedController[i]->run();

      MotorPWM[i].setPWM(MotorDir[i] * speedControllerParam[i].output * Rad2PWM); // Raw
      encoderOld[i] = encoderNew[i];
    }

    // Update wheel speed vector for odometry calculations
    for (int i = 0; i < NumMotors; i++)
    {
      robotWheelSpeed[i] = inputs[i][windowIndex];
    }

    // Calculate the robot's state change
    robotOdomChange = (wheelRadius * kinematikInv * EncoderRadDiff);
    worldOdomChange = robot_vel_to_world_vel(robotOdom[2] + robotOdomChange[2]/2.0, robotOdomChange);

    // Update odometry position
    robotOdom += worldOdomChange;

    windowIndex = (windowIndex + 1) % windowSize;
  }
}

/**
 * @brief Logger task periodically outputs odometry data over serial.
 * 
 * @param pvParameters Task parameters (unused)
 */
void loggerTask(void *pvParameters)
{
  while (true)
  {
    vTaskDelay(pdMS_TO_TICKS(500));
    Serial.print("Odometry: Xt= ");
    Serial.print(robotOdom[0]); // current x-position in meters
    Serial.print(", Yt= ");
    Serial.print(robotOdom[1]); // current y-position in meters
    Serial.print(", Zr= ");
    Serial.println(robotOdom[2]); // current z-rotation in radians
  }
}

/**
 * @brief Arduino setup function, runs once at startup.
 * 
 * Initializes serial, hardware, PID, kinematics, and creates FreeRTOS tasks.
 * Also initializes micro-ROS resources if enabled.
 */
void setup()
{
  Serial.begin(115200);
  initHardware();
  initPID();
  initMatrix();

  xTaskCreatePinnedToCore(
      speedControllerTask,   /* Task function. */
      "speedControllerTask", /* String with name of task. */
      10000,                 /* Stack size in bytes. */
      NULL,                  /* Parameter passed as input of the task */
      5,                     /* Priority of the task. */
      NULL, 1);              /* Task handle. */
#ifdef ROS_EN
  xTaskCreatePinnedToCore(
      ros_task,   /* Task function. */
      "ros_task", /* String with name of task. */
      10000,      /* Stack size in bytes. */
      NULL,       /* Parameter passed as input of the task */
      4,          /* Priority of the task. */
      NULL, 1);   /* Task handle. */
#endif // ROS_EN
  xTaskCreatePinnedToCore(
      loggerTask,   /* Task function. */
      "loggerTask", /* String with name of task. */
      20000,        /* Stack size in bytes. */
      NULL,         /* Parameter passed as input of the task */
      1,            /* Priority of the task. */
      NULL, 1);     /* Task handle. */

#ifdef ROS_EN
  set_microros_wifi_transports(WIFISSID, WIFIPASS, AGENT_IP, AGENT_PORT);

  delay(2000);

  allocator = rcl_get_default_allocator();

  // create init_options
  init_options = rcl_get_zero_initialized_init_options();
  RCCHECK(rcl_init_options_init(&init_options, allocator));

  RCCHECK(rcl_init_options_set_domain_id(&init_options, ROS_DOMAIN_ID));
  RCCHECK(rclc_support_init_with_options(&support, 0, NULL, &init_options, &allocator));

  // create node
  RCCHECK(rclc_node_init_default(&node, "EduRob_Node", "", &support));

  // create subscriber
  RCCHECK(rclc_subscription_init_default(
      &subscriber,
      &node,
      ROSIDL_GET_MSG_TYPE_SUPPORT(geometry_msgs, msg, Twist),
      "cmd_vel"));

  // create publisher
  RCCHECK(rclc_publisher_init_default(&tf_pub, &node, ROSIDL_GET_MSG_TYPE_SUPPORT(tf2_msgs, msg, TFMessage), "tf"));

  // create executor
  RCCHECK(rclc_executor_init(&executor, &support.context, 7, &allocator));
  RCCHECK(rclc_executor_add_subscription(&executor, &subscriber, &msg, &subscription_callback, ON_NEW_DATA));
#endif // ROS_EN
}

/**
 * @brief Arduino main loop, runs repeatedly.
 * 
 * Enables motors and processes ROS incoming commands if enabled.
 */
void loop()
{
  digitalWrite(EnablePIN, HIGH); // Always ensure motors are enabled

  // #############-USER-CODE-START-#####################
  // double tx = 0.0, ty = 0.0, theta = 0.0;
  // robotSpeedSetpoint << tx, ty, theta;

  // #############-USER-CODE-END-#####################

#ifdef ROS_EN
  RCSOFTCHECK(rclc_executor_spin_some(&executor, RCL_MS_TO_NS(10)));
#endif // ROS_EN

  delay(10);
}

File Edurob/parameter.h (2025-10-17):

#ifndef PARAMETER_H
#define PARAMETER_H

#define ROS_EN // Enable ROS2-specific code pathways

// Set EduRob Configuration
#define MECANUM
// #define DIFF
// #define OMNI4
// #define OMNI3



#ifdef ROS_EN
#define ROS_DOMAIN_ID 1
#define WIFISSID "ESPNET"
#define WIFIPASS "espnetwifikey"
#define AGENT_IP "10.0.101.253"
#define AGENT_PORT 8888

#endif


// #############-USER-CODE-START-#####################
#ifdef OMNI4
//############################## 4 Omni Wheels ##############################
static const double wheelRadius = 0.024;     // Wheelradius in meters (Mecanum/4-Omni)
static const double l1 = 0.0825;             // Distance between axels aka "length"
static const double l2 = 0.0825;             // Distance between wheels aka "width"
//###########################################################################
#endif

#ifdef MECANUM
//############################## 4 Mecanum Wheels ##############################
static const double wheelRadius = 0.024;     // Wheelradius in meters (Mecanum/4-Omni)
static const double l1 = 0.1;                // Distance between axels aka "length"
static const double l2 = 0.0865;             // Distance between wheels aka "width"
//###########################################################################
#endif

#ifdef OMNI3
//############################## 3 Omni Wheels ##############################
// static const double wheelRadius = 0.012825;  // Wheelradius in meters (3-Omni)
static const double wheelRadius = 0.019;  // Wheelradius in meters (3-Omni)
static const double l1 = 0.1025;             // Distance between axels aka "length"
static const double l2 = 0.1025;             // Distance between wheels aka "width"
//###########################################################################
#endif

static const float maxTSpeed = 0.4;            // Maximum translational speed in m/s
static const float maxRSpeed = 1.5;            // Maximum rotational speed in rad/s
static const float maxTAccel = 0.7;            // Maximum translational acceleration in m/s²
static const float maxRAccel = 1.5;            // Maximum rotational acceleration in rad/s²
static int EncoderDir[4] = {1, 1, 1, 1}; // Counting direction of encoderchannels (+1 or -1)
static const int MotorDir[4] = {1, -1, -1, 1};   // Direction of motors (+1 or -1)
// #############-USER-CODE-END-#####################

static const int NumMotors = 4;                                          // Number of Motors (Max=4)
static const int sampleTime = 5;                                         // Sample time in ms
static const int gearing = 100.0;                                        // Number of motorrotations per wheelrotation
static const int encoderSteps = 28;                                      // Number of encoder increments per motorrotation
static const double incrementsToRad = 2 * PI / (encoderSteps * gearing); // Conversion from encoder increments to rad
static const double circumference = (2 * PI * wheelRadius);              // Circumference in meters
static const double msToRads = (2 * PI) / circumference;                 // Conversion from m/s to rad/s
static const int nMax = 210;                                             // Maximum revolutions / min
static double Rad2PWM = 100.0 * 60.0 * gearing / (2.0 * PI * nMax);      // Conversion from rad/s to pwm duty cicle



// Motornumbering
// |2|--|1|
//    ||
// |3|--|4|

// Pin definitions

//EdurobV2
static const int PWM_A[4] = {14, 47, 38, 17};  // GPIO PWM channel A
static const int PWM_B[4] = {18, 39, 48, 21}; // GPIO PWM channel B
static const int Enc_A[4] = {4, 2, 41, 7}; // GPIO Encoder channel A
static const int Enc_B[4] = {5, 1, 42, 6};  // GPIO Encoder channel B

static const int EnablePIN = 40;              // Enable Signalpin for motordrivers
 

typedef struct pidParam
{                   // PID Parameters
  double input;     // Input data
  double output;    // Output data
  double setpoint;  // Setpoint
  double p;         // Proportional
  double i;         // Integral
  double d;         // Differential
  int sampleTimeMs; // Sampletime in ms
  double outMin;    // Lower limit of output
  double outMax;    // Upper limit of output
};

#endif // PARAMETER_H

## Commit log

2023-03-20 Initial upload
    [EduRobController.brd, EduRobController.sch]
2023-03-21 Added more infos
    [EduRob_Battery_Compartment_Assembly.STEP]
2023-03-21 Fixed CAD link
2023-07-31 Added Projects "Line Follower" and "SLAM"
    [LIDAR_Adapter v5.step]
2023-11-23 New Connectors and minor changes
    [EduRobController.brd, EduRobController.sch]
2024-01-30 Updated dimensions
    [Edurob_Mecanum_Adapter.step, Edurob_Motor_Mount.step]
2024-05-14 Moved kinematics matrices, added ability to have multiple dimensions for different kinematics, added new Rad2PWM calculation of maximum revolutions, changed min max of PID to avoid overshoot, fixed s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
    [Edurob.ino, parameter.h]
2025-10-02 Added ROS2 Jazzy support, moved from PlatformIO to Arduino for compatibility
2025-10-08 Fix spelling of header file of Arduino library
2025-10-14 Improve odometry updates by using increments
    Directly use the encoder's increments to update the EduRob's odometry state
    without calculating speeds first. This removes timer jitter that would
    interfere with the odometry calculation.
    Rational: Since the increments directly state the wheel's rotations and thereby
    through the inverse kinematics the change in the robot's position there is no
    benefit in first calculating wheel speeds to later use the wheel speed to get
    the state change again.
    [Edurob.ino]
2025-10-14 Do not filter acceleration for cmd_vel
    Since EduRob can not make any assumptions on the source of the /cmd_vel
    messages filtering them removes the ability to quickly stop the robot or do any
    other velocity changes. The velocities are better filtered by the node creating
    the /cmd_vel messages.
2025-10-29 Update README.md
    Updates the README with a Quickstart on how to use the Edurob V2 with ROS2 Jazzy (via micro_ros_agent) or only with the included Arduino Sketch.
2025-11-10 Add LIDAR mount v6 step file for Edurob V2
    [LIDAR_Adapter v6.step]
2025-11-16 Fix ROS_EN
    Fix ROS_EN and make project compilable when ROS_EN is not defined.
    [Edurob.ino]
2026-03-19 Remove EduRob V1 PCB and reference PCB repro
    [EduRobController.brd, EduRobController.sch]
2026-03-19 Make link to PCB repro absolute
2026-03-19 Move CAD to own repro
    [EduRob_Baseplate.STEP, EduRob_Battery_Compartment_Assembly.STEP, EduRob_Battery_Compartment_EjectB.STEP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]
